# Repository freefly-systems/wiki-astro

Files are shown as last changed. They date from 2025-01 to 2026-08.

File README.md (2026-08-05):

# Astro / Astro Max

{% embed url="https://youtu.be/W2aNijm3UPw" %}

The Freefly Astro is a compact professional multi-rotor built for enterprise and industrial work. Flown with the Pilot Pro controller, it runs an enterprise PX4-based flight stack and carries an onboard mission computer, RTK-capable GNSS, and swappable payloads.

This guide will be continuously updated with the latest information.

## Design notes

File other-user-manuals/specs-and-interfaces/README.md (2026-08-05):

---
description: How to integrate Astro intro your custom workflow
icon: bolt
---

# Specs and Interfaces

{% content-ref url="technical-specs.md" %}
[technical-specs.md](technical-specs.md)
{% endcontent-ref %}

{% content-ref url="performance.md" %}
[performance.md](performance.md)
{% endcontent-ref %}

{% content-ref url="drawings-and-cad.md" %}
[drawings-and-cad.md](drawings-and-cad.md)
{% endcontent-ref %}

{% content-ref url="../compliance/" %}
[compliance](../compliance/)
{% endcontent-ref %}

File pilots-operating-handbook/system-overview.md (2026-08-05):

---
icon: book-open-lines
---

# System Overview

<figure>media&token=5d01687a-c96d-4a51-b992-1f1958ca7538"<figcaption></figcaption></figure>

Astro is the next generation of Freefly aircraft, which emphasizes expandability and customization to make sure it can stand up to all challenges thrown its way while still being the reliable workhorse drone that Freefly pilots know and love.

## Key Components

### Astro Aircraft Layout

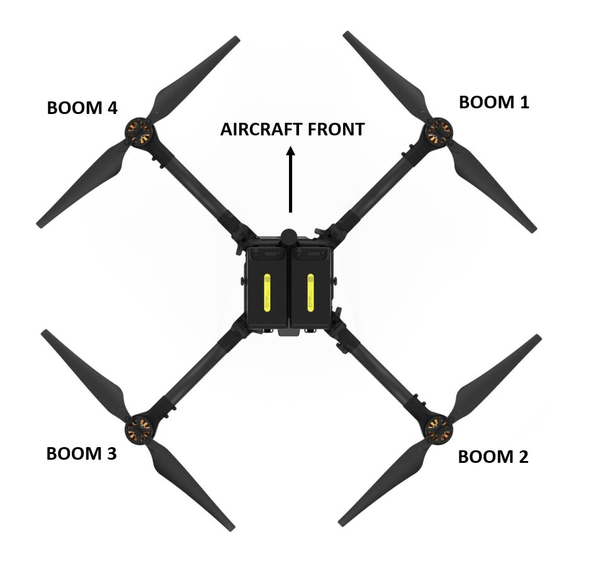
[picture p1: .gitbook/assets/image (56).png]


### Astro Transmitter

{% tabs %}
{% tab title="Pilot Pro" %}
The current iteration of Astro ships with [**Pilot Pro**](https://store.freeflysystems.com/products/pilot-pro)**,** our custom controller. For more information, check the [Pilot Pro wiki](https://freefly.gitbook.io/pilot-pro-public/).

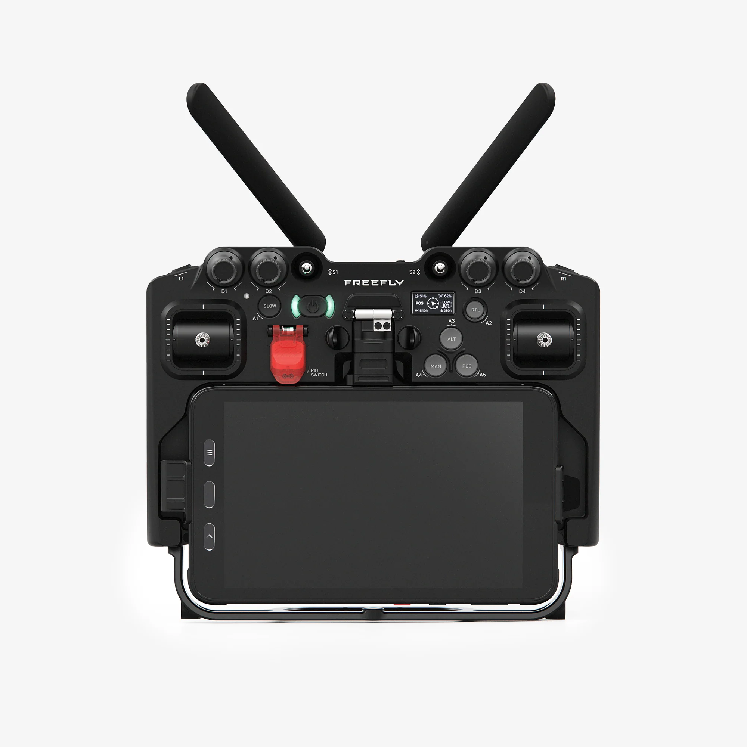
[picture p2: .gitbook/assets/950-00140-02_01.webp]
<figure><figcaption></figcaption></figure>
{% endtab %}

{% tab title="Herelink Controller" %}
Astro shipped with the [Herelink](../other-user-manuals/ecosystem/components/pilot-handsets/#herelink) controller as the pilot handset before late 2023. It runs a custom version of [Auterion Mission Control](essential-software/auterion-mission-control/) as its flight software.

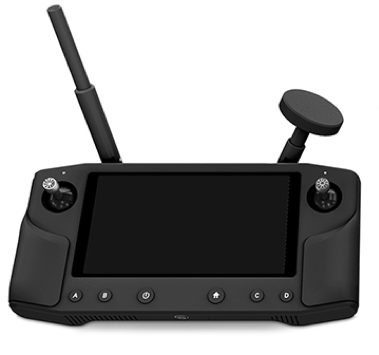
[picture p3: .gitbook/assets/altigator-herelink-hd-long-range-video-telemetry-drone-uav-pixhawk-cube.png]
<figure><figcaption></figcaption></figure>
{% endtab %}
{% endtabs %}

### SuperLight Battery

<figure>media&token=274368b1-176e-472b-a856-2636772e2193"<figcaption></figcaption></figure>

SuperLight Lithium-ion batteries are designed and manufactured by Freefly. You can find more information on the battery in the [SuperLight Battery](https://docs.freeflysystems.com/ecosystem/power/superlight-batteries) section of the wiki.

## Astro LEDs

There are 5 total status LEDs on the Astro. The 4 boom LEDs at the end of each arm show constant lights in most circumstances. By default, the rear two boom LEDs are red, and the front two boom LEDs are green. These LEDs will blink as the battery gets low, and blink quickly if there is an error.

The Astro uses a multi-color status indicator LED to communicate aircraft status on the ground. This LED is located on the front-left boom of the aircraft (pictured below in blue on boom 4). See the table below for complete information on the color codes

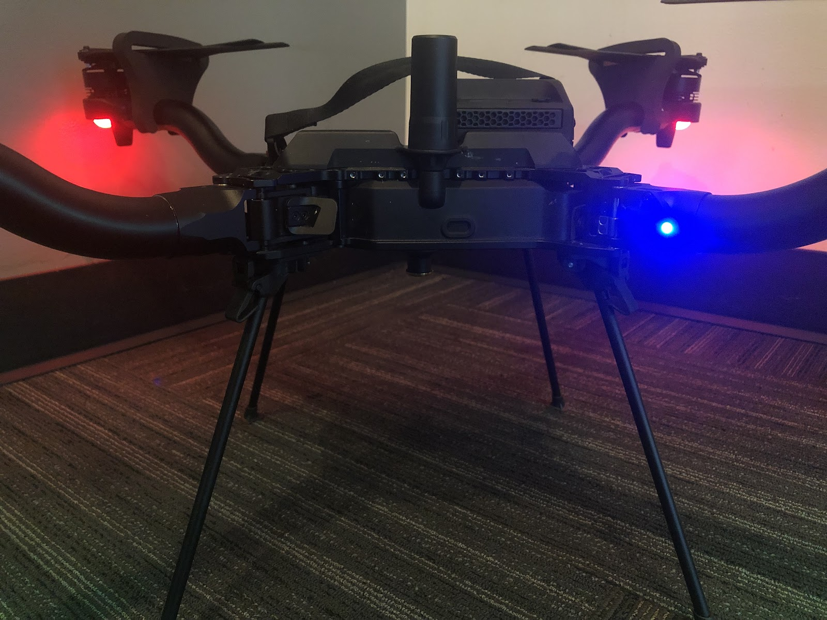
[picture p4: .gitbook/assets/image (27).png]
color code
<figure><figcaption><p>Location of the Status Indicator LED (Blue)</p></figcaption></figure>

### Status Indicator LED Color Codes

<table data-search="false"><thead><tr><th>Color</th><th>Meaning</th><th>Detail</th></tr></thead><tbody><tr><td>Solid Blue</td><td>Armed, No GPS Lock</td><td>Indicates vehicle has been armed and has no position lock from the GPS. Position, Mission and Return flight modes are not available.</td></tr><tr><td>Pulsing Blue</td><td>Disarmed, No GPS Lock</td><td>Indicates vehicle is disarmed and has no position lock from the GPS. Position, Mission and RTL flight modes will not be available until GPS lock is acquired.</td></tr><tr><td>Solid Green</td><td>Armed, GPS Lock</td><td>Indicates vehicle has been armed and has position lock from the GPS. All flight modes are available.</td></tr><tr><td>Pulsing Green</td><td>Disarmed, GPS Lock</td><td>Indicates vehicle is disarmed and has position lock from the GPS. All flight modes will be available.</td></tr><tr><td>Solid Purple</td><td>Failsafe Mode</td><td>Indicates an error has been encountered during flight and the vehicle will activate the Failsafe Action (Return To Launch by default).</td></tr><tr><td>Solid Amber</td><td>Low Battery Warning</td><td>Indicates a battery voltage below threshold.</td></tr><tr><td>Flashing Red</td><td>Error / Setup Required</td><td>Indicates an error, typically an issue with sensor calibration or autopilot configuration. </td></tr></tbody></table>

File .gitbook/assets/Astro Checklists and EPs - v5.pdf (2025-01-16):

Astro Checklists and EPs - v5

1

Before Leaving | | On Return
Astro | Packed | Clean | Everything
Batteries | Charged, Packed | Batteries | Store or charge
Herelink | Charged, Packed | Suite | Verify logs uploaded
Payload | Packed
Computer (optional) | Charged, Packed

Computer tripod (optional)Packed
RTK (optional) | Packed
RTK cable (optional) | Packed
RTK Tripod (optional) | Packed
Setup | | Tear Down
Airspace | Verify available | Flight Batteries | Remove
Astro | Remove from case | Propellers | Fold
Booms | Unfold and lock | Prop-tectors | Install, slide to motor
Prop-tectors | Remove | Booms | Fold
Motors and Props | Spin freely, No Play | Payload | Remove
Payload | Install, configure | Astro | Insert into case
Herelink | Open AMC | Suite | Annotate flights

Pilot Computer, optional Open AMC

| Connect to HereLink
| Connect RTK (optional)

Astro Checklists and EPs - v5

2

Preflight | Emergency Procedures
Herelink Battery above 20% | Low Battery
Pilot Computer Battery above 20% | Aircraft Land
Aircraft position Away from obstacles | Loss of Orientation
Payload Secure | Control Inputs Neutralize
Flight Batteries Charge > 20% | Flight Mode Position
Install and activate | Yaw Nose away
Aircraft Stationary while booting | Roll Small input
Orientation LEDs Dim, Constant | Verify direction
AMC Verify connected | Unexpected Behavior
No warnings | Control Inputs Neutralize
Return altitude set | Flight Mode Position
Geofence (optional) | Aircraft Land
Flight Mode Return, Altitude | Landing Detector Failure
Flight Mode Position | Flight Mode Position or Altitude
Aircraft Verify orientation | Land firmly
Props Verify clear | Flight Mode Manual
Takeoff | Land firmly
Throttle Down + Right (Arm) | Throttle Down + Left, 10 sec
Motors All spin | Loss of Video Signal
Orientation LEDs Bright, Constant | Flight Mode Position
Throttle Advance above center | Visual contact Establish
Astro Climb | Aircraft Orient for reception
Landing | Flight Mode Return
Announce "Landing" | RC Loss of Signal (LOS)
Landing Area Verify clear | Herelink Check Battery
Mode Switch Position | Check Antennas
Astro Touchdown | Flight Mode Return
Throttle Down (Disarm) | Emergency Stop - Manual
Motors All Stop | Flight Mode Manual
Orientation LEDs Dim, Constant | Throttle Down + Left, 10 sec
Post Flight | Emergency Stop - AMC
AMC Check for warnings | AMC App Tap "Armed" (top center)
Aircraft, Props, Motors Inspect for Damage | Hold to confirm E-Stop

Flight Batteries Remove

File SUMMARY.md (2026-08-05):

# Table of contents

* [Astro / Astro Max](README.md)

## Pilot's Operating Handbook

* [Getting Started](pilots-operating-handbook/getting-started.md)
* [System Overview](pilots-operating-handbook/system-overview.md)
* [Flight Part 1 - Flight Modes](pilots-operating-handbook/flight-modes.md)
* [Flight Part 2 - Operation](pilots-operating-handbook/operation.md)
* [Flight Part 3 - Emergency / Advanced](pilots-operating-handbook/emergency-procedures.md)
* [Auterion Software](pilots-operating-handbook/essential-software/README.md)
  * [Auterion Mission Control](pilots-operating-handbook/essential-software/auterion-mission-control/README.md)
    * [AMC - Fly](pilots-operating-handbook/essential-software/auterion-mission-control/amc-fly.md)
    * [AMC - Plan](pilots-operating-handbook/essential-software/auterion-mission-control/amc-plan/README.md)
      * [Transfer Mission Plan and KML Files with Herelink](pilots-operating-handbook/essential-software/auterion-mission-control/amc-plan/transfer-mission-plan-and-kml-files-with-herelink.md)
      * [Terrain Follow](pilots-operating-handbook/essential-software/auterion-mission-control/amc-plan/terrain-follow.md)
      * [Offline Maps](pilots-operating-handbook/essential-software/auterion-mission-control/amc-plan/offline-maps.md)
    * [AMC - Vehicle Setup](pilots-operating-handbook/essential-software/auterion-mission-control/amc-vehicle-setup/README.md)
      * [Advanced Vehicle Setup](pilots-operating-handbook/essential-software/auterion-mission-control/amc-vehicle-setup/advanced-vehicle-setup.md)
      * [Parameters](pilots-operating-handbook/essential-software/auterion-mission-control/amc-vehicle-setup/parameters.md)
    * [AMC - Photos](pilots-operating-handbook/essential-software/auterion-mission-control/amc-photos.md)
    * [AMC - User Account](pilots-operating-handbook/essential-software/auterion-mission-control/amc-user-account.md)
    * [AMC - Settings](pilots-operating-handbook/essential-software/auterion-mission-control/amc-settings/README.md)
      * [Advanced Mode](pilots-operating-handbook/essential-software/auterion-mission-control/amc-settings/advanced-mode.md)
  * [Auterion Suite](pilots-operating-handbook/essential-software/auterion-suite.md)
* [Pro Tips and Limitations](pilots-operating-handbook/limitations.md)
* [Getting Technical Support](pilots-operating-handbook/getting-technical-support.md)

## Maintenance

* [Standard Maintenance Procedures](maintenance/standard-maintenance-procedures/README.md)
  * [Periodic Maintenance](maintenance/standard-maintenance-procedures/periodic-maintenance.md)
  * [Replacing Components](maintenance/standard-maintenance-procedures/replacing-components/README.md)
    * [Replacing Propellers](maintenance/standard-maintenance-procedures/replacing-components/replacing-propellers.md)
    * [Installing a SIM Card](maintenance/standard-maintenance-procedures/replacing-components/installing-a-sim-card.md)
  * [Calibration and Tuning](maintenance/standard-maintenance-procedures/calibration-and-tuning.md)
  * [Controller / Radio Binding](maintenance/standard-maintenance-procedures/controller-radio-binding.md)
  * [SL8/Astro Battery Connectors](maintenance/standard-maintenance-procedures/sl8-astro-battery-connectors.md)
* [Network and Connectivity](maintenance/network-and-connectivity.md)
* [Software Updates](maintenance/software-release-notes/README.md)
  * [Updating Firmware](maintenance/software-release-notes/software.md)
  * [Astro Software v2.2 - What's New](maintenance/software-release-notes/astro-software-v2.2-whats-new.md)
  * [Astro Software v2.0 - What's New](maintenance/software-release-notes/astro-software-v2.0-whats-new.md)
  * [Astro Software v1.7 - What’s New](maintenance/software-release-notes/astro-software-v1.7-whats-new.md)
  * [Astro Software v1.4 - What’s New](maintenance/software-release-notes/astro-software-v1.4-whats-new.md)
  * [Astro Software v1.2 - What’s New](maintenance/software-release-notes/astro-software-v1.2-whats-new.md)
* [FAQ & Troubleshooting](maintenance/faq-and-troubleshooting.md)

## Other User Manuals

* [Ecosystem](other-user-manuals/ecosystem/README.md)
  * [Components](other-user-manuals/ecosystem/components/README.md)
    * [Batteries](other-user-manuals/ecosystem/components/batteries.md)
    * [Pilot Pro Controller](other-user-manuals/ecosystem/components/pilot-pro-controller.md)
    * [Herelink Handset (Legacy)](other-user-manuals/ecosystem/components/pilot-handsets/README.md)
      * [Herelink Controller Maintenance](other-user-manuals/ecosystem/components/pilot-handsets/herelink-controller-maintenance/README.md)
        * [Updating Herelink Software](other-user-manuals/ecosystem/components/pilot-handsets/herelink-controller-maintenance/updating-herelink-software.md)
        * [Switching to Freefly Updater](other-user-manuals/ecosystem/components/pilot-handsets/herelink-controller-maintenance/switching-to-freefly-updater.md)
        * [Removing/Reinstalling the Herelink Cover](other-user-manuals/ecosystem/components/pilot-handsets/herelink-controller-maintenance/removing-reinstalling-the-herelink-cover.md)
    * [Vibration Isolators](other-user-manuals/ecosystem/components/vibration-isolators.md)
    * [Skyview Payload Mount](other-user-manuals/ecosystem/components/skyview-payload-mount.md)
    * [GNSS Base Stations](other-user-manuals/ecosystem/components/gnss-base-stations.md)
  * [Development Tools](other-user-manuals/ecosystem/development-tools/README.md)
    * [MavSDK](other-user-manuals/ecosystem/development-tools/mavsdk.md)
    * [Software Interfaces](other-user-manuals/ecosystem/development-tools/software-interfaces.md)
    * [Payload Mounting Interfaces](other-user-manuals/ecosystem/development-tools/payload-mounting-interfaces.md)
    * [Electrical Interfaces](other-user-manuals/ecosystem/development-tools/electrical-interfaces.md)
    * [Onboard Computer](other-user-manuals/ecosystem/development-tools/onboard-computer.md)
  * [Esri ArcGIS Flight (Site Scan)](other-user-manuals/ecosystem/esri-arcgis-flight-site-scan/README.md)
    * [1 - Setup and Connecting to Astro](other-user-manuals/ecosystem/esri-arcgis-flight-site-scan/1-setup-and-connecting-to-astro.md)
    * [2 - Preflight and Mission Planning](other-user-manuals/ecosystem/esri-arcgis-flight-site-scan/2-preflight-and-mission-planning.md)
    * [3 - Flying a Mission with Astro](other-user-manuals/ecosystem/esri-arcgis-flight-site-scan/3-flying-a-mission-with-astro.md)
    * [4 - Post-Flight and Image Processing](other-user-manuals/ecosystem/esri-arcgis-flight-site-scan/4-post-flight-and-image-processing.md)
    * [Global Settings](other-user-manuals/ecosystem/esri-arcgis-flight-site-scan/global-settings.md)
  * [DroneDeploy](other-user-manuals/ecosystem/dronedeploy.md)
* [Specs and Interfaces](other-user-manuals/specs-and-interfaces/README.md)
  * [Technical Specs](other-user-manuals/specs-and-interfaces/technical-specs.md)
  * [Performance](other-user-manuals/specs-and-interfaces/performance.md)
  * [Drawings and CAD](other-user-manuals/specs-and-interfaces/drawings-and-cad.md)
* [Travel and Shipping](other-user-manuals/travel-and-shipping.md)
* [Compliance](other-user-manuals/compliance/README.md)
  * [FAA Remote Identification (RID)](other-user-manuals/compliance/faa-remote-identification-rid.md)
  * [DIU Blue sUAS](other-user-manuals/compliance/diu-blue-suas.md)
* [Legal](other-user-manuals/legal.md)

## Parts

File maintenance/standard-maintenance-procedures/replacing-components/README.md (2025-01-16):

# Replacing Components

{% content-ref url="../../../other-user-manuals/ecosystem/components/pilot-handsets/herelink-controller-maintenance/removing-reinstalling-the-herelink-cover.md" %}
[removing-reinstalling-the-herelink-cover.md](../../../other-user-manuals/ecosystem/components/pilot-handsets/herelink-controller-maintenance/removing-reinstalling-the-herelink-cover.md)
{% endcontent-ref %}

{% content-ref url="replacing-propellers.md" %}
[replacing-propellers.md](replacing-propellers.md)
{% endcontent-ref %}

{% content-ref url="installing-a-sim-card.md" %}
[installing-a-sim-card.md](installing-a-sim-card.md)
{% endcontent-ref %}

## Replacement Parts

If you need to purchase spare or replacement parts, please go to [store.freeflysystems.com](http://store.freeflysystems.com) to purchase our standard parts.&#x20;

For any specific replacement needs or issues, please contact support@freeflysystems.com or [submit a direct ticket](https://freeflysystems.com/contact) with your request.

## Fastener Specifications

{% hint style="warning" %}
**Use Of Thread locker**

Bolts and screws used in the daily use of this aircraft do not require threadlocking compound. This includes the screws securing the vibration isolation system and the  landing gear parts.

However, for the structural fasteners described in parts of this section, blue Loctite 243 compound or equivalent is required. Apply sparingly to the threads before insertion.
{% endhint %}

{% hint style="warning" %}
**Fastener Installation**

The Freefly hex drivers included with Astro are designed to limit the torque that can be applied to each bolt or screw and help prevent stripping the fastener head.

Thread all fasteners into their respective holes until snug (when the fastener head bottoms out and lightly clamps the two mating parts together).

To prevent excessive tightening and damaging the fastener or parts, twist the driver from the smaller diameter knurled section of the tool between your thumb and index finger for small fasteners (under size M3) or with your thumb and two forefingers for larger fasteners (size M3 and larger).
{% endhint %}

#### Fastener Torque Values

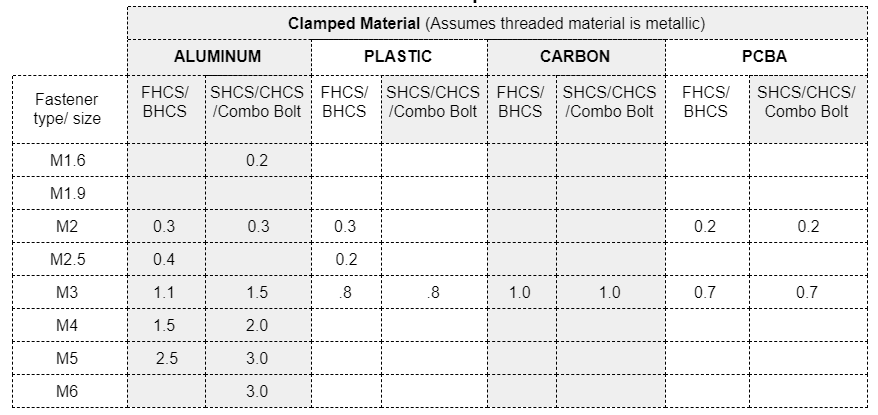
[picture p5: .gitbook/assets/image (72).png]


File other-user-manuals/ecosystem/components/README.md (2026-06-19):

# Components

{% content-ref url="batteries.md" %}
[batteries.md](batteries.md)
{% endcontent-ref %}

{% content-ref url="pilot-handsets/" %}
[pilot-handsets](pilot-handsets/)
{% endcontent-ref %}

{% content-ref url="vibration-isolators.md" %}
[vibration-isolators.md](vibration-isolators.md)
{% endcontent-ref %}

{% content-ref url="gnss-base-stations.md" %}
[gnss-base-stations.md](gnss-base-stations.md)
{% endcontent-ref %}

{% content-ref url="../../../maintenance/standard-maintenance-procedures/replacing-components/replacing-propellers.md" %}
[replacing-propellers.md](../../../maintenance/standard-maintenance-procedures/replacing-components/replacing-propellers.md)
{% endcontent-ref %}

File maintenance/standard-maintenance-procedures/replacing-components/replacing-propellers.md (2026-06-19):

# Replacing Propellers

{% embed url="https://www.youtube.com/watch?v=ifPETgSw0Oc" %}

{% hint style="warning" %}
Ensure rotation direction is correct. Always replace propellers with a set intended to rotate in the same direction (clockwise or counter-clockwise). We suggest replacing one propeller assembly at a time to minimize potential for mix-ups, rather than removing all propellers at once.
{% endhint %}

{% hint style="info" %}
Always replace both propeller blades as a set. They are a matched and balanced pair, with matching serial numbers. This is to reduce vibration.
{% endhint %}

#### Astro vs Astro Max Motors

Before you consider replacing props, it is important to identify the which Astro motors you have.&#x20;

The **Astro** is equipped with Freefly _F45_ motors, where the **Astro Max** has a newer Freefly _7010_ motor.

In addition to providing more thrust than the prior generation motor, the Astro Max 7010 motors have a different mounting pattern for props than the F45 motor. Reference the image below to identify which one you have.

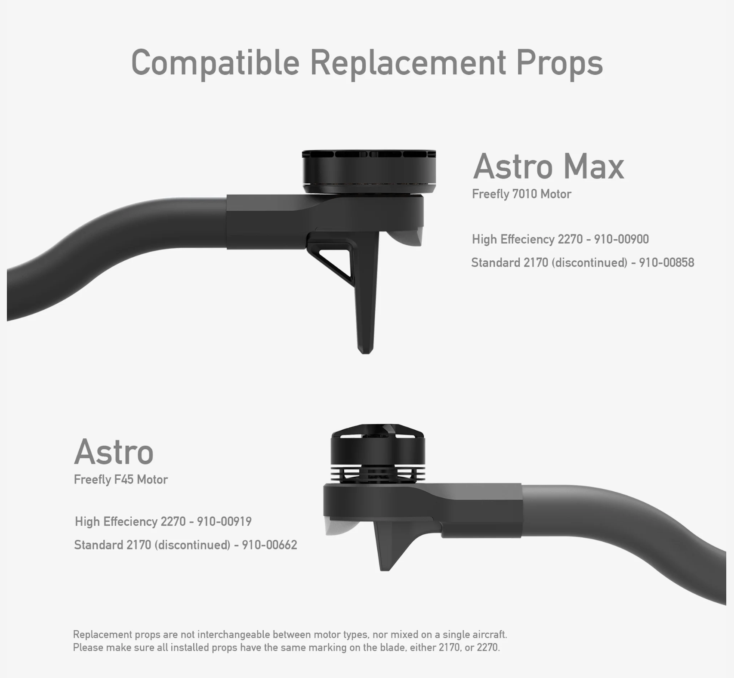
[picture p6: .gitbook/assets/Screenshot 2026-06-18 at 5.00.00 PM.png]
<figure><figcaption></figcaption></figure>

#### Identifying your current props

Legacy props are 21" long and marked with "2170".

High efficiency props are 22" long, and marked with "2270".&#x20;

Example of a 2270 CCW prop:\
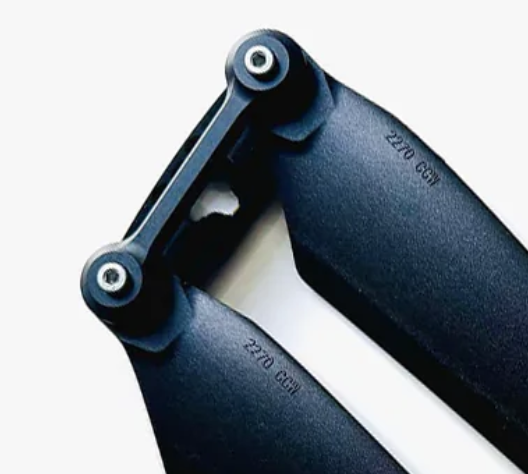
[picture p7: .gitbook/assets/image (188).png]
&#x20;

#### **Which props do I need?**

* Since we no longer sell the 21" (2170) props, we only carry the high-efficiency 22" (2270) props.
* Depending on the motor you have, the 22" props will come with the appropriate mounting hardware.
  * If you have the Astro with F45 motors, you have the legacy Astro and will need to get the [Astro Legacy Spare Props](https://store.freeflysystems.com/collections/astro/products/astro-legacy-spare-propeller-set-2270-high-efficiency) (2270)
  * If you have the Astro with 7010 motors, you have Astro Max, and will need to get the [Astro Max Spare Props](https://store.freeflysystems.com/collections/astro/products/astro-max-spare-propeller-set-high-efficiency) (2270)<br>

#### How many props do I need?

1. If you want to upgrade your legacy Astro (F45 motors) to maximize flight time, you'll need to purchase two sets of the 2270 props. We recommend a third set to have a spare set in your kit.
2. If you just need a replacement prop (CW or CCW) and have 21" props on your Astro marked with "2170" on the blade, you'll need to purchase two sets of the 2270 props so you can replace the props on all four motors.&#x20;
3. If your Astro already has 22" props marked with "2270" on the blade, just purchase what you feel comfortable having for spares. Most people have one set (one each CW & CCW) in their kit.&#x20;

#### Steps to replace props on legacy Astro (F45 motors)

1. Remove fasteners between the prop hub and the motors: (x4) M3x10 bolts.
2. Remove the old propeller assembly.
3. Fit the new propeller assembly.
4. Apply Loctite 243 or equivalent to all screws before installing. torque to 1.5 Newton meters.
5. Reinstall (x4) M3x8 bolts.

<figure>media&token=7237d1a8-d1b5-465c-ac06-25bf0994b76e"<figcaption><p>Propellers are labelled with their orientation, Clockwise (CW) or Counter-clockwise (CCW).</p></figcaption></figure>

The correct direction of the propellers is shown below. Please note the arrow indicating the front of the Astro, which is easily identified by the cylindrical antenna.

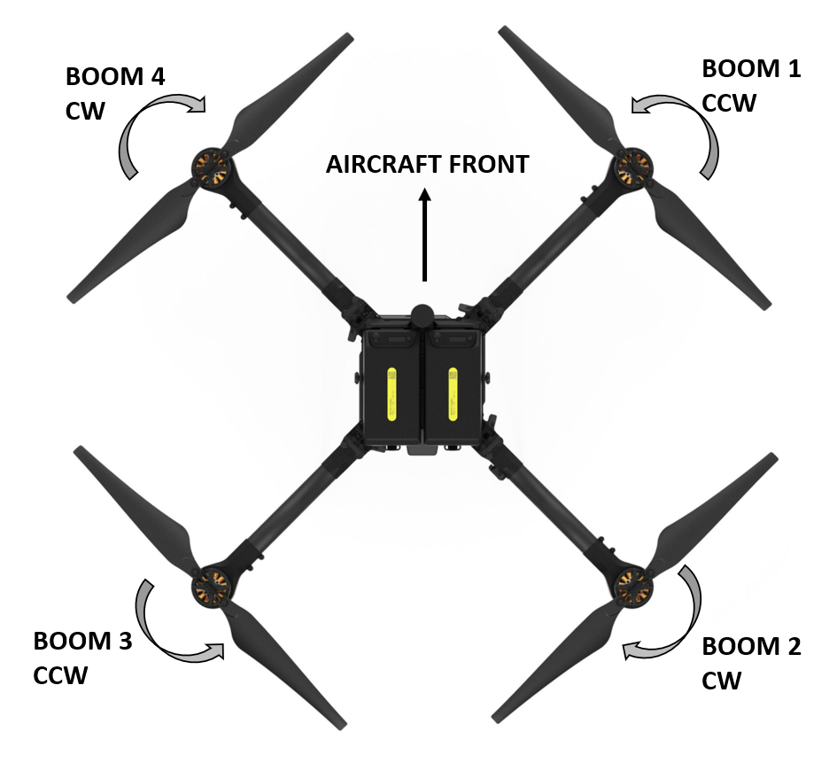
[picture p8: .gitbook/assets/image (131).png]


### Prop Tension

Each blade of the propeller assembly should move freely with a small amount of resistance. It should not be difficult to fold the prop manually, and the force of gravity should be enough to pivot the blade at the bolt if the aircraft is rotated.

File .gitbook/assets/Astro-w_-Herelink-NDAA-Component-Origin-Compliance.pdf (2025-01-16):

# Astro w /Herelink NDAA sec. 848 Compliance Specification Sheet

Specified Components | Sub component | Specific Product Used | Supplier | Country | Included | Required | Assembly | Testing | Validation
Flight controller | Flight controller hardware | Skynode | Freefly | Taiwan | Yes | Yes | Taiwan | USA | USA
| Flight control firmware | Firmware | Freefly | USA | Yes | Yes | N/A | USA | USA
Radios | Control & Video Transmitter/Receiver | Herelink | ProfiCNC | China | Yes | Yes | ProfiCNC | USA | USA
Data transmission devices | LTE Modem | Skynode | Freefly | Taiwan | Yes | No* | Taiwan | USA | USA
Cameras | N/A | N/A | N/A | N/A | N/A | N/A | N/A | N/A | N/A
Ground control system | Pilot Controller | Herelink | ProfiCNC | China | Yes | Yes | N/A | USA | USA
| Ground Station Computer (operator supplied) | Computer or tablet | Operator supplied | N/A | No | No | N/A | N/A | N/A
Operating software | Pilot’s Control Software | Auterion Mission Control | Auterion | Switzerland | Yes | No | N/A | Auterion | Auterion
Network connectivity | LTE | T-Mobile SIM | T-Mobile | Various | Yes | No | Various | Various | Various
Data storage | Local log storage | microSD card | Sandisk | Various | Yes** | Yes | Various | USA | USA
| Cloud Storage | Auterion Suite | Auterion | Switzerland | No | No | N/A | USA | USA

### *LTE Connectivity is data plan based and is not required for operation **SD card is for local storage only and is not physically accessible to users

## July 12th, 2021

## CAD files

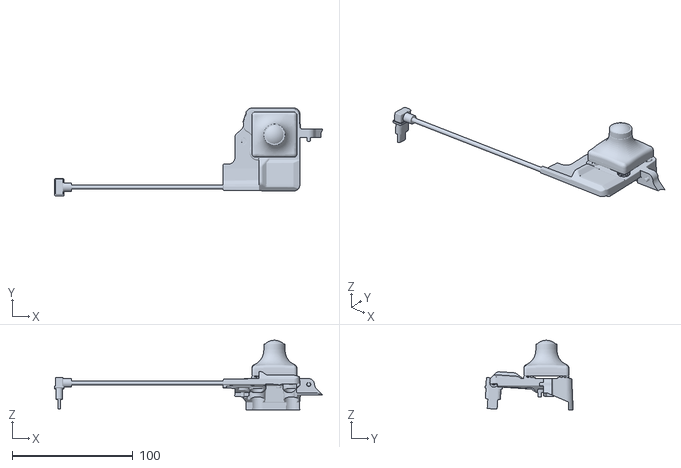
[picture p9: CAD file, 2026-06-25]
.gitbook/assets/Astro FPV System.STL
221.6 x 73.0 x 57.5

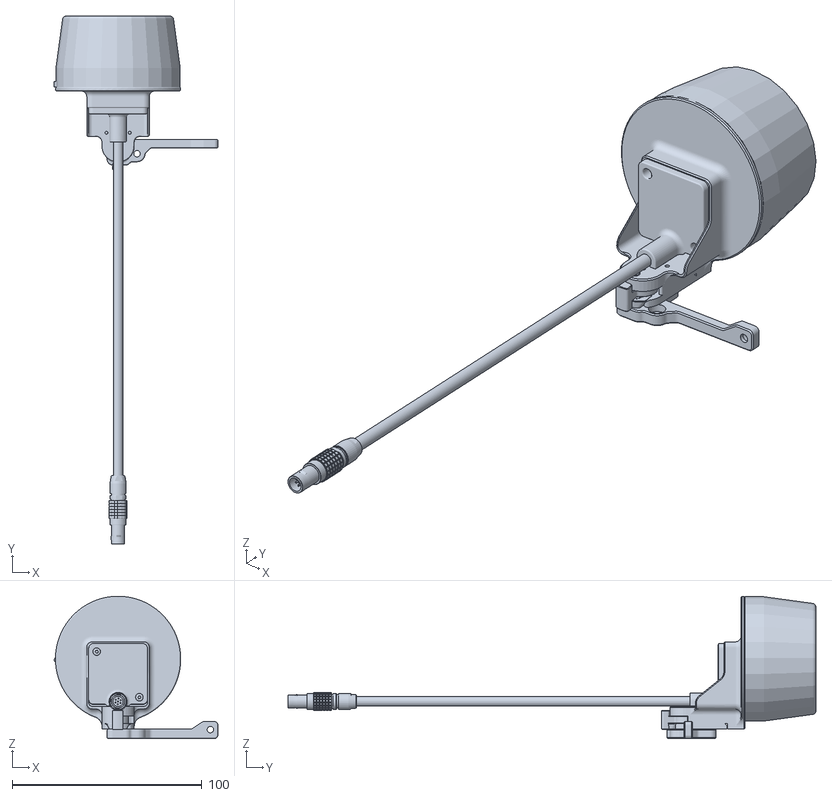
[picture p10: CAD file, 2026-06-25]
.gitbook/assets/Flux GNSS Module and Astro Mount.STL
86.4 x 278.1 x 75.1

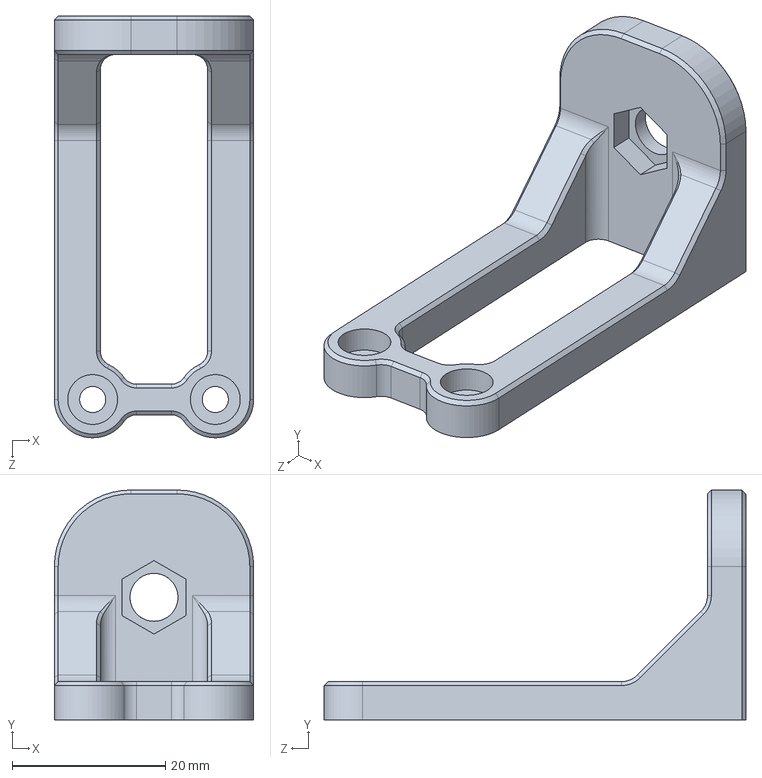
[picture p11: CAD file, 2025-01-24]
.gitbook/assets/432-00086 Antenna Mount Astro REV_01.STEP
26.0 x 30.0 x 55.0 mm

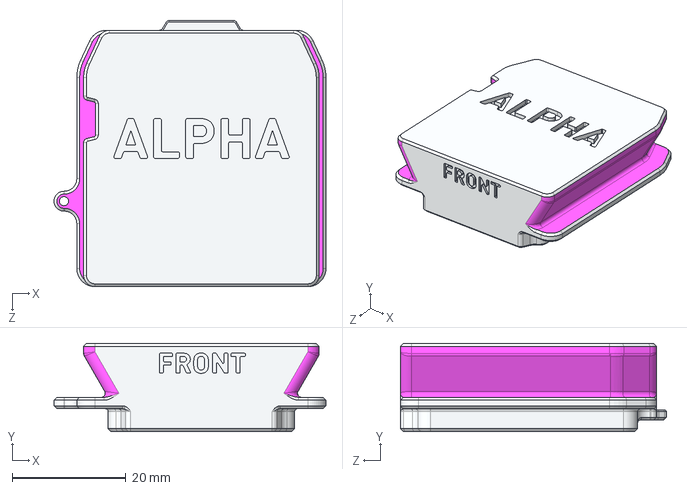
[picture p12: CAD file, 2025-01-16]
.gitbook/assets/ALPHA_410-01094 Dovetail Mount Universal with Passthrough.STEP
47.8 x 15.5 x 46.8 mm

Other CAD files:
.gitbook/assets/432-00086 Antenna Mount Astro REV_01.STL

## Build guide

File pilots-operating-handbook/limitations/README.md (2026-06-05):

# Pro Tips and Limitations

It is possible to operate Astro close to the limits of performance by maintaining awareness of the performance envelope, how the aircraft behaves if the limits are exceeded, and best practices for operating in harsh environments.

This page reflects the limitations of the most current version. As the Astro platform matures, limitations are likely to change. For major changes that may affect these limitations, check the [release notes](https://freefly.gitbook.io/astro-public/products/astro/maintenance-manual/software-release-notes).

***

## Troubleshooting

Visit our [Troubleshooting Spreadsheet](https://docs.google.com/spreadsheets/d/1DXkk0BmRx9qLbjpBt2KgKYFOQhEGUTcyyQB6rOmb4ac/edit#gid=528435697) to look into additional solutions if you aren't finding what you're looking for on the wiki.&#x20;

***

## Flight Control

For all flight modes except Manual, at altitudes below 2 meters, the tilt angle is reduced to 12 degrees and vertical speed is reduced to 0.7 m/s.

The purpose is to prevent tip-overs while landing but has the side effect of reducing speed if flying below the takeoff point (e.g. surveying from a high vantage point). We are working to correct this behavior.

***

## Continuous Flight

If you have 8 SL8 batteries, 6 SL8 chargers, and electricity at the location of your flight, you can continuously charge 6 batteries at a time while flying Astro, allowing for uninterrupted flight for as long as you need. If you are flying without a payload, you will only need 6 batteries and 4 chargers.&#x20;

{% hint style="warning" %}
In hot conditions, you will likely need an additional 2 batteries, as it may take some time to cool the recently flown batteries to an acceptable charging temperature (50°C).&#x20;
{% endhint %}

***

## Radio Range and Interferences

Operating with a weak signal, whether due to interference or long range, can cause loss of link with the aircraft, which will engage failsafes. If you anticipate a weak signal situation, double-check that failsafes are set appropriately.

### Range

The range of Herelink and the Doodle radios on Astro is approximately 2 km in ideal conditions, assuming there are no interferences and the antennas are positioned correctly.

### Antenna Positioning

{% hint style="warning" %}
This is one of the simplest to miss and impact the range of the flight
{% endhint %}

#### **Pilot Pro**

Both the Doodle and Herelink radio modules on Pilot Pro use two blade antennas that are omni directional. It is important to follow these basic guidelines:

* Antennas should both point in the same direction.&#x20;
* Antennas should point towards ground for best signal quality in most situations.

<figure><figcaption></figcaption></figure>

#### **Herelink GCS (Legacy):**&#x20;

Herelink GCS has two types of antennas.&#x20;

* Patch antenna (with a circular disk on top) is a directional antenna and should be pointed toward the aircraft
* Other antenna is omni-directional and it should be positioned pointing towards the ground or sky

### Interferences

Range can be reduced by radio interference from other sources like wifi networks. Obstacles like trees and buildings in close proximity to the controller or Astro, as well as directly between the two, can dramatically reduce range.

### Multiple Aircraft

* Astro's Doodle radio configuration runs on dedicated peer to peer channels. In order to fly multiple Astros in the same airspace, make sure to scan channels and then set each Astro Doodle to a different channel.
* Astro's Herelink radios are channel hopping by default. 4 aircraft can fly simultaneously in the same airspace in practice. If more aircraft are present, interference can cause loss of radio link and control.
  * If using the legacy Herelink GCS, you can set each Herelink to be on a dedicated channel
  * If using the Pilot Pro with the Herelink radio, this feature is not yet available.

### High Power Radio Interference

Avoid using high-power, low-frequency radio transmitters (such as the RFD 900) mounted to Astro, as it can disrupt the normal function of the aircraft. For more information,  see this [service bulletin](https://freeflysystems.com/knowledge-base/astro-sb002-high-power-radio-astro-interference).&#x20;

***

## Environment

### Temperature

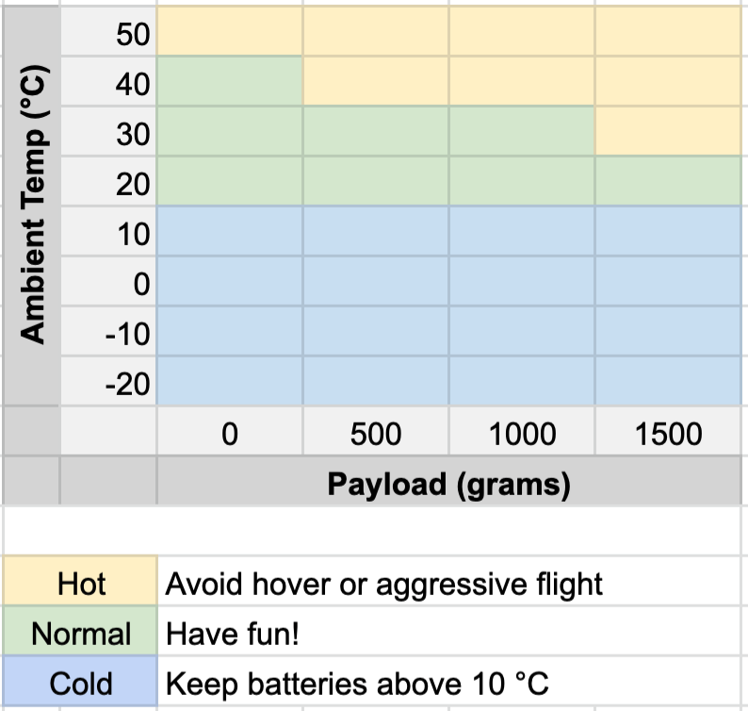
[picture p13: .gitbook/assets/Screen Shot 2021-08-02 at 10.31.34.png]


Astro can operate between -20 and 50 C. Position mode and survey flying are normal throughout the range. However, care is needed to operate at low and high temperatures.

Yellow region: Hovering and aggressive flights may give overtemp warnings. Follow the warning instructions.

Blue region: If batteries become too cold, state of charge will decline quickly and aircraft will enter Return or Land mode. Keep batteries warm, above 10 °C at takeoff, then self-heating will keep them warm.&#x20;

{% tabs %}
{% tab title="Tips for operating in hot environments" %}
At high temperatures, the limiting factors are motor and battery temperatures. AMC will display a warning if the motors or batteries become too hot. Heed the warnings! Astro operates normally in forward flight up to 15 m/s with a full payload of 1500 grams.&#x20;

Cooling air is your friend. The motors get much more cooling air in forward flight than in a hover. Overheat errors may occur when hovering because there is less airflow, or when flying aggressively because heating increases with current.

Batteries may require cooling before charging. Bring an extra set of batteries and chargers to enable continuous flying. If you connect batteries to the charger while cooling, they will automatically begin charging as soon as they have cooled sufficiently.

Keep the equipment out of prolonged direct sunlight, especially the Herelink. Herelink will shut down if it overheats, and it does not give a warning.
{% endtab %}

{% tab title="Tips for operating in cold environments" %}
At low temperatures, the battery cell temperature is the key limiting factor. When the cells themselves are below 10 °C (ambient air can be down to -20 °C), the built-in battery management system's (BMS) state of charge (SoC) algorithm has reduced accuracy. The SoC may decrease to zero suddenly. If this happens, [low battery failsafes](../emergency-procedures.md#low-battery) (RTL and Land) will be triggered, causing the aircraft to climb or descend suddenly.

These failsafes can be overridden by selecting another flight mode (override by moving the sticks is not available during a failsafe). The battery will not cut off power output in the air, however low temperatures generally reduce capacity which will reduce flight time.

If the batteries are 10 °C or warmer at the start of a flight, heating from discharge will keep them warm enough to fly.

To keep batteries warm, charge them in a heated environment and store them in an insulated container (a cooler works well)**In rare cases propellers can experience icing, this occurs when ice begins to form on the tips and underside of the blades due to temperature and humidity. This will cause the props to become unbalanced, increasing drag and reducing lift. Flying with iced blades can be dangerous and is not advised.**
{% endtab %}
{% endtabs %}

{% hint style="info" %}
Keep the Herelink handset out of direct sunlight. It can operate at up to 50C ambient _if its plugged in for charging and in the shade._ \
\
For the best performance in hot or cold weather, we recommend charging the Herelink during use. Under very hot or cold weather Herelink's battery performance can drop quickly and can cause it to shutdown.
{% endhint %}

{% hint style="warning" %}
Herelink will shut down if the internal temperature increases over 55C, and it does not give a warning. Direct sunlight can increase the temperature of the Herelink beyond this limit very quickly.&#x20;
{% endhint %}

### Wind

Operating Astro at winds greater than 8-10m/s can be dangerous. Keep in mind that the wind speed at higher altitudes is typically much higher. In high wind, AMC will show a warning.

Flying Astro is high wind is not advised. If the wind speed is a significant fraction of [Astro's top speed](https://freefly.gitbook.io/astro-public/astro/specs-and-interfaces/performance#flight-speeds), control authority will be diminished in all flight modes.

When Astro is not flying, fold the props and install the propeller protectors. If the wind blows through open props, it can cause them to spin up dangerously.

### Rain and Dust

Astro can operate in moderate rain (approximately 3 mm per hour). [USGS has a guide (scroll to bottom)](https://water.usgs.gov/edu/activity-howmuchrain-metric.html) to help translate between forecasts like "shower" or "drizzle" to accumulation amount.

Battery connectors cannot be mated while wet or containing debris. We recommend compressed air to clean the connectors.

#### Tips for operating in Rainy and Dusty environments.

Rain in particular increases the risk of electrical malfunction because it can lead to short circuits

Dust carries a risk of mechanical malfunction because it can enter the motors and obstruct rotation.

Both of these conditions carry an increased risk of malfunction and danger. It is difficult to judge the exact amount of precipitation, and the amount can vary without warning during the course of a flight. Therefore, we recommend avoiding situations that endanger people.

***

## Voltage Mismatch

If the two batteries powering Astro have a voltage difference of more than 2.0V, a voltage mismatch error will occur. 2V is roughly a 25% difference in the batteries' states of charge.&#x20;

***

## Magnetic Interference

In a situation where there is a magnetic interference that is preventing the aircraft to figure out its heading before takeoff, you are presented with options:

* Move away from any potential sources of magnetic interference, like metal or water. In most cases, moving the Astro a few feet away will allow it to get a better magnetic reading to figure out the heading, and position mode will become available for takeoff.&#x20;
* Take off in altitude mode. Shortly after flying in altitude mode, GPS heading will be locked and you can then switch to position mode.

{% hint style="warning" %}
Be aware that flying in Altitude Mode does introduce additional risk. If the aircraft loses connection with the controller, it will not hold its horizontal position which may result in a crash if control is not re-established quickly. &#x20;
{% endhint %}

***

.

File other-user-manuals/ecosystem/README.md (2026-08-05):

---
icon: gears
---

# Ecosystem

{% content-ref url="components/" %}
[components](components/)
{% endcontent-ref %}

{% content-ref url="../../pilots-operating-handbook/essential-software/" %}
[essential-software](../../pilots-operating-handbook/essential-software/)
{% endcontent-ref %}

{% content-ref url="development-tools/" %}
[development-tools](development-tools/)
{% endcontent-ref %}

## Astro Integration Sketchpad

{% file src="../../.gitbook/assets/Astro Integration Sketchpad v1.pdf" %}
Astro Integration Sketchpad
{% endfile %}

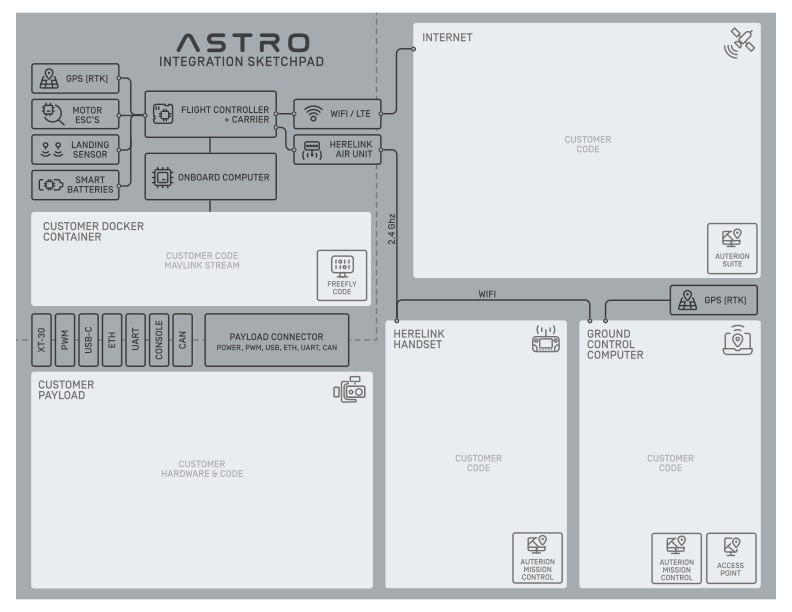
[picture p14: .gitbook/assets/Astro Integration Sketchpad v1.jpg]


Here's a printable template to diagram ideas for working with Astro. We're looking forward to [seeing your plans!](https://freeflysystems.com/contact)

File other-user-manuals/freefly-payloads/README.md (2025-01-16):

# FREEFLY PAYLOADS

{% content-ref url="lr1-payload/" %}
[lr1-payload](lr1-payload/)
{% endcontent-ref %}

{% content-ref url="a7r4-payload/" %}
[a7r4-payload](a7r4-payload/)
{% endcontent-ref %}

{% content-ref url="wiris-pro-payload/" %}
[wiris-pro-payload](wiris-pro-payload/)
{% endcontent-ref %}

{% content-ref url="ventus-ogi-payload/" %}
[ventus-ogi-payload](ventus-ogi-payload/)
{% endcontent-ref %}

{% content-ref url="fpv-camera.md" %}
[fpv-camera.md](fpv-camera.md)
{% endcontent-ref %}

{% content-ref url="workflows-maintenance-updates/" %}
[workflows-maintenance-updates](workflows-maintenance-updates/)
{% endcontent-ref %}

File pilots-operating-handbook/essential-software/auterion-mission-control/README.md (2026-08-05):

# Auterion Mission Control

Auterion Mission Control (AMC) is a ground control station application for pilots. Use it to plan and fly missions, control the aircraft in flight, and configure Astro on the ground. AMC comes pre-installed on Pilot Pro and is also available as a desktop app for PC, Mac, and Linux.&#x20;

See Auterion's full documentation for AMC [here](https://docs.auterion.com/vehicle-operation/auterion-mission-control).

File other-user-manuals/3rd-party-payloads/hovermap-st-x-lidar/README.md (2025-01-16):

# Hovermap ST-X Lidar

The Emesent Hovermap ST-X lidar is an excellent payload for creating detailed, accurate lidar point clouds.

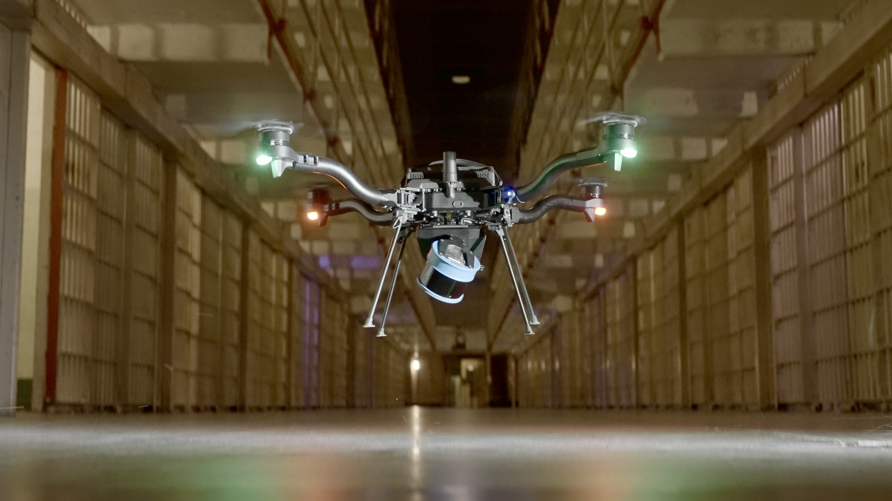
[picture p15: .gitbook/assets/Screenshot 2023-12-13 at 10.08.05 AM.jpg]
<figure><figcaption><p>Astro + Hovermap ST-X flying inside Alcatraz Cell House </p></figcaption></figure>

### Setting up Hovermap

{% content-ref url="hovermap-setup-on-astro.md" %}
[hovermap-setup-on-astro.md](hovermap-setup-on-astro.md)
{% endcontent-ref %}

### Operation modes

Hovermap can interact with Astro as a passive payload, for mapping applications that can be flown with good GPS signal in open spaces with few obstacles. &#x20;

{% content-ref url="mapping-with-hovermap.md" %}
[mapping-with-hovermap.md](mapping-with-hovermap.md)
{% endcontent-ref %}

Hovermap can also use the lidar data of the environment around Astro, and build a 3D model in real time. It can use that data for obstacle avoidance, and even allow Astro to autonomously explore GPS-denied areas like under bridges and inside tunnels and mines.&#x20;

{% embed url="https://drive.google.com/file/d/1E1IJqVptU_CEoJ5mKBL6M3PxekiDd3TQ/view?usp=drive_link" %}
Bridge scan with Hovermap ST-X
{% endembed %}

{% embed url="https://youtu.be/045shpvB-m4" %}
Astro navigating using Hovermap Assisted Mode
{% endembed %}

{% content-ref url="assisted-autonomous-flight.md" %}
[assisted-autonomous-flight.md](assisted-autonomous-flight.md)
{% endcontent-ref %}

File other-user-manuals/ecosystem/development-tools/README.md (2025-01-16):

# Development Tools

{% content-ref url="mavsdk.md" %}
[mavsdk.md](mavsdk.md)
{% endcontent-ref %}

{% content-ref url="software-interfaces.md" %}
[software-interfaces.md](software-interfaces.md)
{% endcontent-ref %}

{% content-ref url="payload-mounting-interfaces.md" %}
[payload-mounting-interfaces.md](payload-mounting-interfaces.md)
{% endcontent-ref %}

{% content-ref url="electrical-interfaces.md" %}
[electrical-interfaces.md](electrical-interfaces.md)
{% endcontent-ref %}

{% content-ref url="onboard-computer.md" %}
[onboard-computer.md](onboard-computer.md)
{% endcontent-ref %}

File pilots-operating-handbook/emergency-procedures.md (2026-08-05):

---
icon: drone-front
---

# Flight Part 3 - Emergency / Advanced

## General Guidance

**Human safety must be the top priority. Aircraft can be replaced. People cannot. Always prioritize the safety of yourself and others over the preservation of aircraft or equipment.**

Emergency situations are dynamic events, that will not often conform perfectly to the categories listed below. A thorough understanding of aircraft systems, proficiency in piloting the aircraft, and sound judgment will allow you to bring about the best possible outcome in an emergency.

The likelihood of an emergency can be reduced substantially through [proper aircraft maintenance](/broken/pages/-MfEfk7y0P474WN5vrmM), the use of [checklists for normal procedures](/broken/pages/-MfEfCAXYq5xABmbFcTc#checklists), and careful pre-flight planning. The likelihood of a safe flight often depends on the diligence of the pilot, both before taking off and during operation.

In general, if an emergency occurs, three basic actions can be applied to most situations:

1. Maintain aircraft control — Small emergencies can quickly escalate if the pilot is distracted attempting to troubleshoot the problem. Always maintain visual contact with the aircraft during an emergency to reduce the likelihood of losing orientation.
2. Analyze the situation — Once the aircraft is stabilized, assess the cause of the emergency.
3. Take appropriate action — In many cases, the appropriate action will be to land the aircraft as soon as possible. Aircraft can be replaced.&#x20;

### Return Mode

Do not be over-reliant on [Return Mode](operation.md#return) in emergency situations. The cause of the emergency may degrade performance or disable Return Mode. For example, loss of GPS disables Return Mode.

{% hint style="warning" %}
Depending on what Astro firmware version you're on, you may or may not be able to move sticks to interrupt Return Mode&#x20;

Before Astro version 1.4.6, moving the flight sticks on the controller will interrupt Return and Mission mode.&#x20;

For Astro version 1.4.6-1.5.18, moving the flight sticks will not interrupt these modes.&#x20;

In 1.6.14 and later this setting was re-introduced as an opt-in setting that's disabled by default, and by default stick movements will not interrupt Return Mode

This change was made as a response to feedback that accidental stick movements were interrupting these flight modes erroneously. To change this behavior, you can toggle [Advanced Mode](https://freefly.gitbook.io/astro-public/astro/pilots-operating-handbook/software/auterion-mission-control/amc-vehicle-setup/advanced-vehicle-setup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) and change the COM\_RC\_OVERRIDE parameter to 1 in Vehicle Setup.
{% endhint %}

## Emergency Procedure Checklists

The [Astro checklists](https://freefly.gitbook.io/astro-public/products/astro/pilots-operating-handbook/flight#checklists) contain concise instructions to follow to mitigate risk in the event of an in-flight emergency. Some of these situations are discussed in more detail below.

{% tabs %}
{% tab title="Orientation Loss" %}
### Loss of Orientation

If orientation is lost, neutralize inputs and activate position mode. Then work to identify the front of the aircraft.

We recommend identifying the front of the aircraft via a "guess and check" method of small roll right inputs alternating with yawing the aircraft 90 degrees at a time. We recommend a roll input rather than pitch because at a distance it is easier to see lateral motion than fore/aft motion.

If it is not possible to identify orientation, and it is safe to activate Return Mode, do so. By default in Return Mode, after climbing, the aircraft will yaw to put the front toward the direction of flight.

Resume flying or land as necessary.
{% endtab %}

{% tab title="Unexpected Behavior" %}
### Unexpected Aircraft Behavior

If Astro behaves unexpectedly, do the following: neutralize inputs, activate Position Mode, and observe the aircraft. If it is still flying in an uncommanded manner in Position or Altitude Mode, switch to Manual Mode.&#x20;

In some cases, unexpected behavior is due to degraded GPS signal or erroneous sensor readings (e.g. compass error). In such cases, Return Mode may not behave reliably. Manual Mode does not rely on these sensors.

Land as soon as possible.
{% endtab %}

{% tab title="Landing Detector Failure" %}
### Landing Detector Failure

If the aircraft touches down, but hops back up into the air several times, or sits on the ground with the props continuing to spin, the autopilot may not have detected a landing. Climb and retry landing with a greater downward velocity.

{% hint style="info" %}
Landing the aircraft firmly will give the accelerometers and gyroscopes a sufficient contrast between flight and landing.
{% endhint %}

If an attempted landing is unsuccessful in Position and Altitude mode, land in Manual Mode.

If an attempted landing is unsuccessful in Manual Mode, perform an [Emergency Stop](operation.md#emergency-stop) with the aircraft on the ground or as close as possible.
{% endtab %}

{% tab title="GPS Loss" %}
### Loss of GPS

If GPS is lost, flight modes that rely on GPS (Position, Return, Mission, etc) will not be available. If the aircraft is in Position mode when GPS is lost, the autopilot will switch to Altitude Mode. If the aircraft is in Return or Mission modes when GPS is lost, it will automatically start landing. Landing can be overridden by the pilot by changing modes to Altitude or Manual modes.

{% hint style="info" %}
It is the pilot's responsibility to be proficient with Altitude and Manual Mode and to have the aircraft configured to behave safely if GPS is lost.
{% endhint %}

Examples of behavior without GPS:

* If GPS is not available upon arming, no Home Point is set, and Return Mode is not available. Even if GPS becomes available while flying, Return Mode will not be available.
* If the pilot commands Return Mode, the aircraft will remain in Altitude or Manual Mode, and an error will be displayed on the pilot handset.
* If Land Mode is activated (e.g. by a failsafe), the aircraft will descend as though in Altitude mode, maintaining a consistent descent but drifting with the wind.
* If GPS is lost in Position, the aircraft will display a warning and switch flight mode to either Altitude Mode or Manual Mode, depending on the degradation of the signal and other sensors
* If GPS is providing altitude information (e.g. while using RTK GPS), and GPS is lost, the ability of Altitude Mode to accurately maintain altitude may be affected.
{% endtab %}

{% tab title="RC Loss of Signal (LOS)" %}
### RC Loss of Signal (LOS)

RC Loss of Signal (LOS) can occur if the pilot handset signal is degraded or stops, or if Astro does not receive the signal due to distance or interference (e.g. from obstacles or other radio signals).

If the signal is lost longer than the RC Timeout, a failsafe action will be triggered. The RC Timeout is quite short by default: 0.5 seconds. The pilot may not have time to react before the failsafe action is activated. By default, the failsafe action is Return Mode.

If the signal is lost, check the pilot's handset power and [antenna orientation](../other-user-manuals/ecosystem/components/pilot-handsets/#antennas). Antenna orientation is especially important when Astro is far from the pilot.

If the signal is recovered, the pilot will be able to take control via moving the sticks or pressing a flight mode button.

{% hint style="info" %}
RC Loss of Signal (LOS) is differentiated from Data Link Loss. LOS refers to the stream of SBUS data containing the pilot's inputs. Data Link refers to the stream of MavLINK messages. Astro routes both data streams through a single radio system. Please note that the AMC app needs to be in the foreground on the pilot handset during operation; Data Link will fail after 30 seconds and trigger a failsafe if the AMC app is closed or running in the background.&#x20;
{% endhint %}
{% endtab %}

{% tab title="Video Loss" %}
### Loss of Video Signal

Loss of Video Signal can occur if the aircraft flies out of range or if it flies behind an object that interrupts the signal. Maintaining visual contact is the preferred method to re-establish control of the aircraft, either with the pilot seeing the aircraft or by the use of a visual observer.

Yawing the aircraft can help signal reception if the body of the aircraft is blocking the line of sight between the transmitter and receiver antennas.

If video signal or visual contact cannot be re-established, enable Return Mode to bring the aircraft back to signal reception range.

{% hint style="danger" %}
It is the responsibility of the pilot to see and avoid other aircraft, people, or obstacles. Always maintain a direct line of sight with Astro during flight, use visual observers as operations require, and follow local regulations regarding see-and-avoid requirements.
{% endhint %}
{% endtab %}
{% endtabs %}

## Emergency Stop

{% hint style="danger" %}
#### As a last resort, if it is not possible to land or control the aircraft, perform an Emergency Stop. If performed while flying, this will cause the aircraft to crash. Perform the Emergency Stop as far away from people as possible.
{% endhint %}

{% tabs %}
{% tab title="AMC" %}
### Emergency Stop - AMC

In AMC on the pilot handset or PC, tap the "Armed" button at the top center of the screen to display the Emergency Stop dialogue. Hold the Emergency Stop button for 4 seconds. This works on the pilot handset or PC.

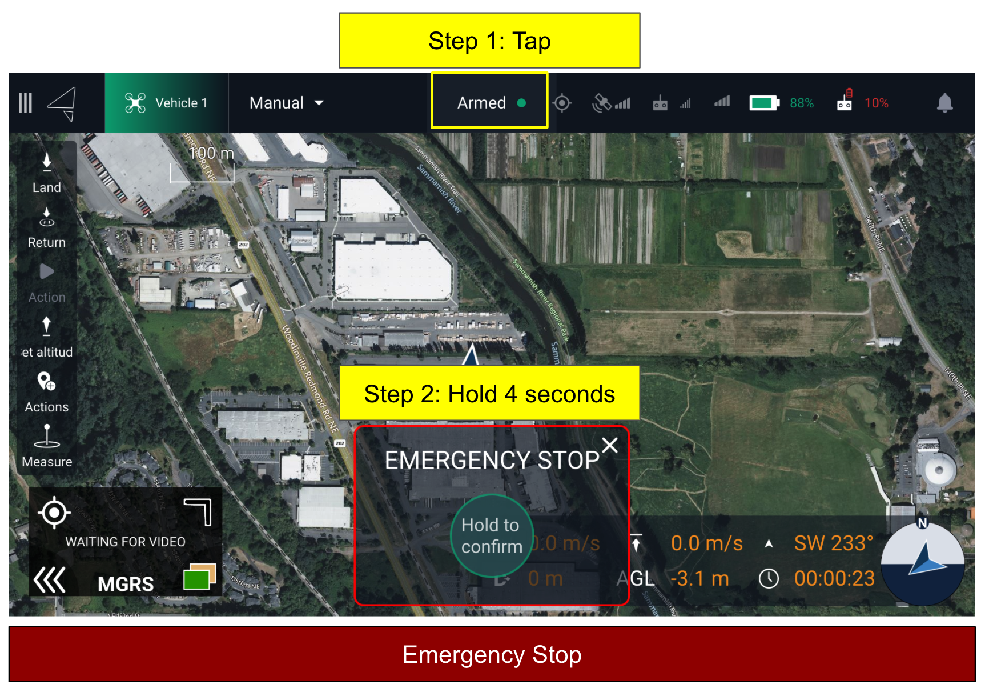
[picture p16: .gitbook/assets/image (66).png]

{% endtab %}

{% tab title="Manual Override" %}
### Emergency Stop - Manual Override

In Manual Mode, hold the throttle stick down and left for 10 seconds.

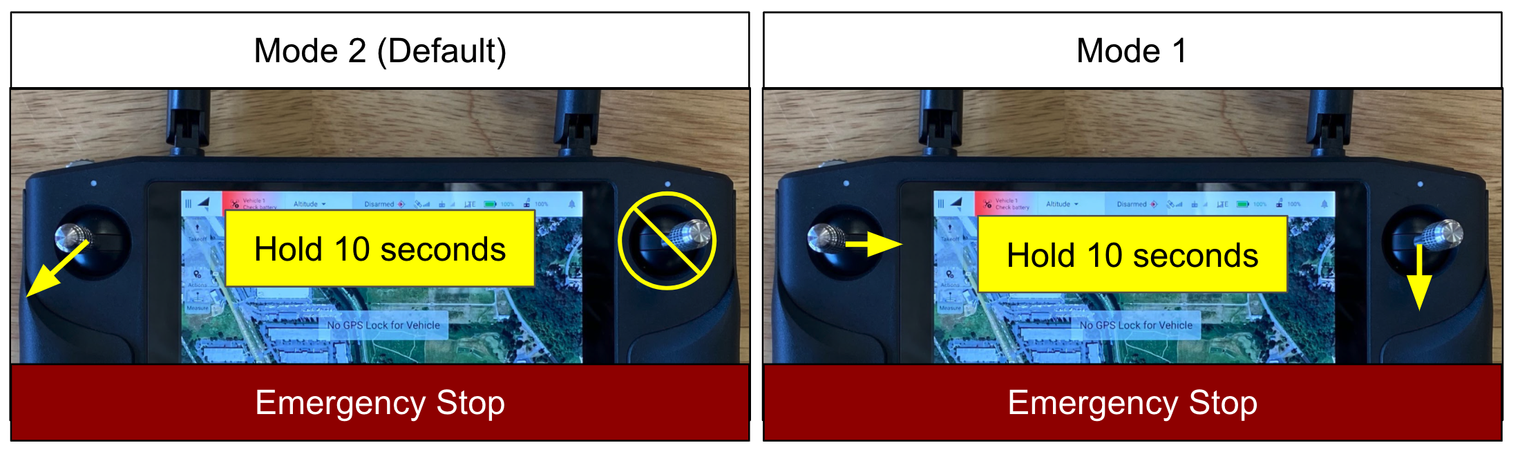
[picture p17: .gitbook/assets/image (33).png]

{% endtab %}
{% endtabs %}

## Failsafes

Failsafe behavior and settings are configured in AMC. The [AMC documentation ](https://docs.auterion.com/vehicle-operation/settings-and-maintenance/safety)covers each failsafe and related settings in detail.

Some failsafes are discussed briefly below.

{% hint style="warning" %}
We strongly recommend using the default settings, changing only Return Altitude, unless you are an expert user and have tested the effect of changes thoroughly.
{% endhint %}

{% tabs %}
{% tab title="Low Battery" %}
### Low Battery

Battery level is evaluated from the State of Charge (SoC, e.g. 72%), not voltage (e.g. 23 Volts).

As the battery level becomes low, the autopilot can take action. The default settings do not interfere until the battery becomes quite low. Additionally, low battery failsafes are only able to estimate how long it will take the aircraft to return to the home point. This means it is the pilot's responsibility to be aware of the battery level and ensure the aircraft is on the ground.

<table><thead><tr><th width="257.3333333333333">State</th><th>SoC (default)</th><th>Action (default)</th></tr></thead><tbody><tr><td>Warning</td><td>20%</td><td>Warning: Flash boom LEDs</td></tr><tr><td>Critical (>200m)</td><td>17-15%</td><td>Return Mode</td></tr><tr><td>Critical (&#x3C;200m)</td><td>10%</td><td>Return Mode</td></tr><tr><td>Emergency</td><td>6%</td><td>Land Mode</td></tr></tbody></table>

{% hint style="info" %}
When activated by a low battery failsafe, Return and Land Mode cannot be overridden by stick movement. They can be overridden by pressing a flight mode button (e.g. Position).
{% endhint %}
{% endtab %}
{% endtabs %}

## Error and Warning Indication&#x20;

The aircraft communicates the presence of errors and warnings primarily through Auterion Mission Control (AMC) [status indicators](https://docs.auterion.com/auterion-mission-control/fly/fly-view-ui-overview#vehicle-status-indicators-top-bar) on the pilot handset or PC. Many messages are accompanied by an audible message (e.g. "Return Flight Mode"). Additionally, Astro boom LEDs will flash when the battery level is low.&#x20;

Status messages, including errors and warnings, are stored in Flight Logs. After any emergency, review the log to determine the source of the problem.

If the meaning of an error or warning is not clear, please [contact Freefly Support](https://freeflysystems.com/support/astro-support). Share as much detail as possible, including [sharing the flight log](essential-software/auterion-suite.md#flight-logs).

## Advanced Arming Methods

| Method | Input |
| --- | --- |
| AMC App, pilot handset | Tap the Arm button (top center) and hold to confirm. |
| Mission | If a mission starts with the takeoff command, and the aircraft is disarmed, the aircraft will arm itself when the mission is initiated. |

{% hint style="info" %}
Arming via the AMC app in Manual Mode is not recommended. In Manual Mode, the aircraft should be armed while the throttle stick is held at the minimum position. This is difficult to achieve while using an app GUI.
{% endhint %}

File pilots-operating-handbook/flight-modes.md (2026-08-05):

---
icon: drone-front
---

# Flight Part 1 - Flight Modes

### Flight Modes

{% embed url="https://www.youtube.com/watch?v=vJHQdul398g" %}

{% hint style="info" %}
Note that this video features the legacy Herelink controller with the original Astro. However, the flight modes and their behavior are unchanged unless otherwise noted in this guide.&#x20;
{% endhint %}

Astro offers several flight modes with varying levels of assistance to the pilot.

Flight mode can be changed via the buttons on the Pilot Pro/Herelink or the AMC app on the handset/PC. See the documentation for the equipment you're using to become familiar with the buttons/switches involved.

{% tabs %}
{% tab title="Pilot Pro" %}
<figure><figcaption><p>Manual mode switch buttons on the Pilot Pro controller</p></figcaption></figure>
{% endtab %}

{% tab title="Herelink Controller" %}
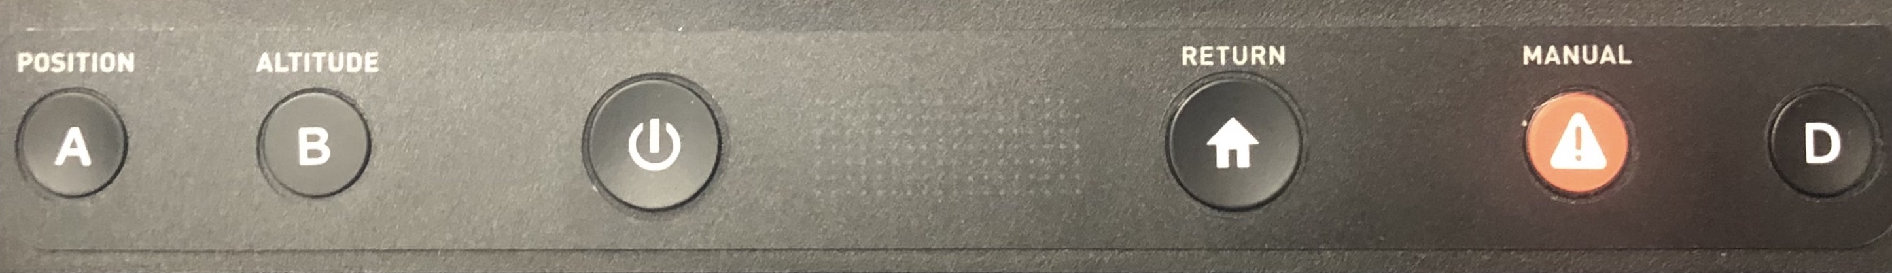
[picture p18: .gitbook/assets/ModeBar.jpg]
<figure><figcaption><p>Manual mode switch buttons along the bottom of the Herelink controller.</p></figcaption></figure>
{% endtab %}
{% endtabs %}

{% hint style="success" %}
Manual Mode may be necessary to react to emergency situations. Pilots should be proficient in Manual Mode. Position, Altitude, and Return Mode are assistive only and are not a replacement for pilot skill and preparedness.&#x20;
{% endhint %}

{% hint style="warning" %}
Always neutralize the control input sticks on the pilot handset when switching between control modes to prevent unexpected aircraft movement.
{% endhint %}

### Pilot-controlled Modes

{% tabs %}
{% tab title="Position" %}
<figure><figcaption><p>Position Mode Button on Pilot Pro</p></figcaption></figure>

In Position Mode, when the sticks are centered, the aircraft will maintain its position over a point on the ground and maintain altitude, correcting for disturbances.

In Position Mode, the pitch/roll stick commands the speed of the drone relative to the ground. The further upward the pitch/roll stick, the faster Astro will fly forward. When the pitch/roll stick is pulled downward, Astro will fly backward. Similarly, the pitch/roll stick will move the drone in the left and right directions when moved to the left and right.

The throttle stick commands vertical speed. The further upward the throttle stick, the faster Astro will climb. Conversely, the lower the throttle stick position, the faster Astro will descend. Deflecting the throttle stick left and right controls the yaw rate, with the speed of rotation proportional to stick deflection.

{% hint style="info" %}
Position Mode requires a strong GPS signal. If a weak signal is present, Astro will not enter Position Mode.&#x20;

If the signal deteriorates, such as near buildings or under dense tree cover, the aircraft will automatically revert to Altitude mode.
{% endhint %}

{% hint style="danger" %}
Flight using Position Mode in areas of degraded GPS signal, such as near buildings or under dense tree cover, is not recommended. The automatic reversion to Altitude Mode can cause unexpected, abrupt changes in flight behavior.
{% endhint %}
{% endtab %}

{% tab title="Altitude" %}
<figure><figcaption><p>Altitude Mode Button on Pilot Pro</p></figcaption></figure>

Similar to Position mode, the pitch/roll stick moves Astro laterally relative to the ground and the throttle stick commands vertical speed and yaw. However, while the drone can hold its vertical position using the barometer, lateral speed is not controlled by the autopilot in Altitude mode. Astro will drift with the wind, will not stop immediately after lateral movement, and will probably not hold a single point above the ground without pilot input.&#x20;

{% hint style="info" %}
The aircraft holds altitude above Mean Sea Level (MSL) by default. It is not aware of terrain height changes or obstacles without additional configuration and equipment.
{% endhint %}
{% endtab %}

{% tab title="Manual" %}
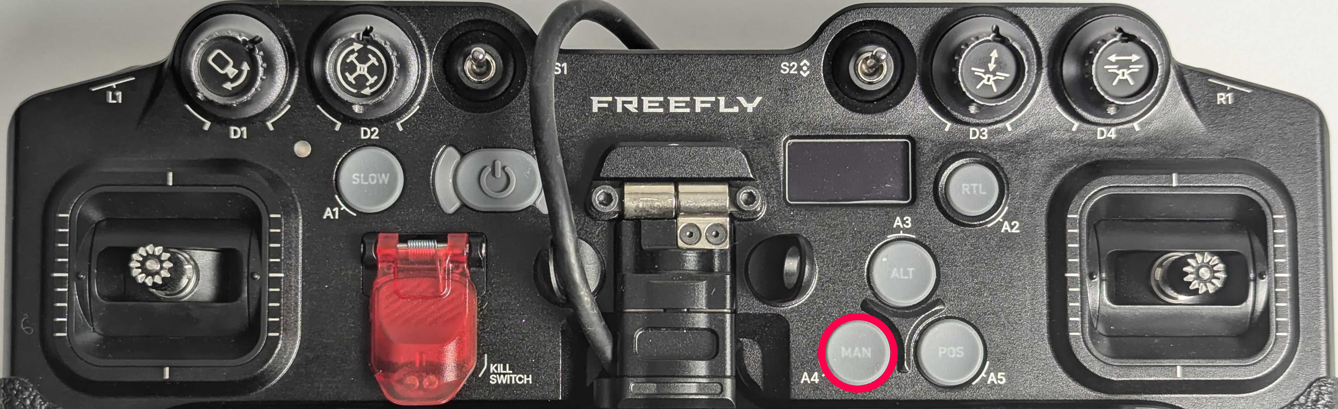
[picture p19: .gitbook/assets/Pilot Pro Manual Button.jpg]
<figure><figcaption><p>Manual Mode Button on Pilot Pro</p></figcaption></figure>

In Manual Mode, when the pitch and roll stick is centered, the aircraft will attempt to remain level and will drift with the wind. The aircraft will require constant throttle adjustment to hold altitude.

In Manual Mode, the pitch and roll stick controls the aircraft angle. The further upward the pitch stick, the further Astro will tilt forward. When the pitch stick is pulled downward, Astro will tilt backward. Similarly for roll in the left and right directions. Lateral speed is not controlled by the autopilot.

The throttle stick controls motor speed directly. Deflecting the throttle stick left and right controls the yaw rate. The speed of yaw rotation is proportional to stick deflection.

#### Manual Mode Settings

The hover throttle setting controls the amount of thrust Astro produces when the throttle stick is centered. The default setting of 34% will hover the aircraft with no payload. A setting of approximately 40% will hover with 1500 grams of payload.&#x20;

Adjust this setting in AMC on the pilot handset or PC:

1. Enable [Advanced Mode ](https://freefly.gitbook.io/astro-public/pilots-operating-handbook/essential-software/auterion-mission-control/amc-vehicle-setup/advanced-vehicle-setup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)
2. Vehicle Setup > Tuning<br>

#### Learn Manual Mode

{% embed url="https://www.youtube.com/watch?v=3eNAD1Ip-9s" %}
{% endtab %}

{% tab title="Position Slow" %}
<figure><figcaption><p>Position Slow Mode Button on Pilot Pro</p></figcaption></figure>

Position Slow acts just like regular Position Mode, but helps to give your flying more control over speed of movement. With the dials on the top of the Pilot Pro, you can now adjust velocity rates on the fly! Whether flying for tower inspections or a cinematic sweep, Position Slow helps give finesse to the pilot to achieve this with ease.&#x20;

{% hint style="info" %}
The gimbal's dial on the left is always active regardless of mode
{% endhint %}

{% hint style="warning" %}
Position Slow was added in Astro v1.4.6 when the Pilot Pro was introduced and has not been tested on the Herelink controller. While it may be accessible depending on software version, you will not have options to change speeds dynamically that you do on the Pilot Pro. To map Position Slow to the D button, open AMC and under Advanced > Flight Modes, set Flight Mode 5 to Position (Slow). Next, enter the Herelink settings by swiping down from the top of the screen and clicking the Herelink stats. Go to the "BUTTONS" tab and change "D short press" from channel 10 to 14, then hit save.
{% endhint %}
{% endtab %}
{% endtabs %}

### Autonomous Modes

{% tabs %}
{% tab title="Return" %}
<figure><figcaption><p>Return Mode Button on Pilot Pro</p></figcaption></figure>

Return Mode commands Astro to climb to the Return Altitude, fly back to the Home Point in a straight line, and land. Return Mode requires GPS.

Return Altitude is set by the pilot at AMC > Vehicle Setup > Safety. Please note that if Astro is above the Return Altitude when Return Mode is initiated, it will maintain altitude instead of dropping to the return altitude.&#x20;

The Home Point is set to the GPS coordinates where Astro is armed. Home Point is reset every time Astro is armed.

By default, Return Mode is activated automatically by some Failsafes.

{% hint style="warning" %}
Before every flight, think through the path the aircraft will take if Return Mode is activated, and adjust settings to arrange for safe behavior.

For example, activating Return Mode while flying under an obstacle lower than the Return Altitude will cause a collision when the aircraft attempts to climb to Return Altitude. In some cases, it may be possible to set a lower Return Altitude, and in other cases, it may not be possible to use Return Mode.
{% endhint %}

{% hint style="info" %}
It is possible to change from Return to Position Mode by moving the sticks, except if Return Mode was activated by the low battery failsafe. In that case, press another flight mode button to change out of Return Mode.
{% endhint %}

In most cases, RTL mode will travel to the predetermined RTL altitude, travel over the home point, and automatically descend to land. However, if the aircraft is close to the home point, the behavior will be slightly different in order to save time and reduce the amount of distance Astro will need to move.

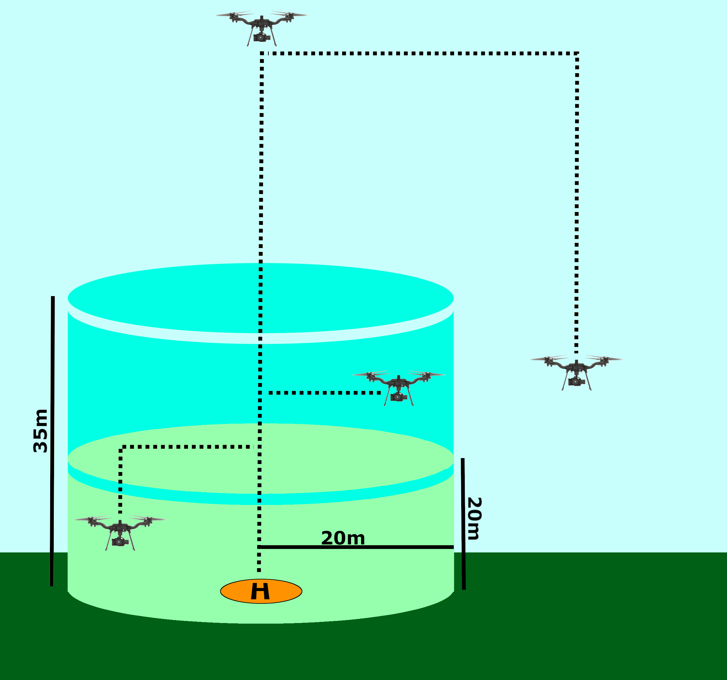
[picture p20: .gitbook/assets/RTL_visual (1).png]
<figure><figcaption></figcaption></figure>

* If Astro is directly over the home point at the time of RTL, it will land without gaining altitude regardless of its current altitude.&#x20;
* If Astro is within a few meters of the home point, it will move directly above the home point and begin landing.
* If Astro is within 20m altitude and less than 20m ground distance from the home point, it will go to 20m altitude, move over the home point, and land.
* If Astro is between 20-35m altitude and less than 20m ground distance from the home point, it will maintain altitude, move over home point, and land.
* If Astro is more than 35m altitude or more than 20m ground distance from the home point, it will go to the set RTL altitude, move over the home point, and land.

&#x20;
{% endtab %}

{% tab title="Takeoff" %}
Takeoff Mode arms the aircraft, automatically climbs to the Takeoff Altitude, and enters [Hold Mode](https://docs.px4.io/v1.12/en/flight_modes/hold.html) (a.k.a. loiter or hover).

Takeoff Mode can be engaged via the button in the AMC app Fly view, optionally changing Takeoff Altitude via the slider, then holding/sliding to confirm. Takeoff Mode can also be engaged during a mission, for example as the first command.

{% hint style="info" %}
Takeoff Mode requires a GPS lock.
{% endhint %}

{% hint style="info" %}
Moving the sticks while in Hold Mode (i.e. after the aircraft has finished climbing) will cause a change to Position Mode. This makes it easy to take control without pressing the Position Mode button.
{% endhint %}
{% endtab %}

{% tab title="Landing" %}
### Landing Mode

Landing Mode causes Astro to descend and land directly below the position where Land Mode is engaged. Once on the ground, Astro will disarm.

Landing mode can be engaged via the button on the AMC app Fly screen. You'll need to hold the button down to confirm the switch.&#x20;

Landing Mode is often the last command in a mission. It can also be engaged by a failsafe, such as low battery level, or loss of signal.

{% hint style="info" %}
Land Mode requires GPS when engaged manually.&#x20;

When Land Mode is engaged by a failsafe, and GPS is not available, the autopilot behavior will be similar to Altitude Mode and the aircraft may drift horizontally as it descends.
{% endhint %}

{% hint style="info" %}
Moving the sticks will cause a change to Position Mode unless Landing Mode is engaged by a Failsafe (e.g. critical battery level). See the [Safety and Failsafes section](/broken/pages/-LaNWMwiqb_UzRIMSvUW) for more details.

When activated by a low battery failsafe, Return and Landing Mode cannot be overridden by stick movement. They can be overridden by pressing a flight mode button (e.g. Position).
{% endhint %}
{% endtab %}

{% tab title="Mission" %}
Mission Mode allows Astro to execute a predefined autonomous waypoint mission that has been uploaded to the flight controller via AMC. For more information on all the different options and abilities built into the Mission Mode, see the AMC docs, sections such as:

* [Planning a mission](https://freefly.gitbook.io/astro-public/astro/pilots-operating-handbook/software/auterion-mission-control/amc-plan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)
* [Flying a mission](https://docs.auterion.com/auterion-mission-control/fly/flying-a-mission)
* [Remove a mission from the aircraft](https://docs.auterion.com/auterion-mission-control/plan/plan-ui-overview#file-sync-tools)

{% hint style="danger" %}
Starting a mission can cause the aircraft to arm itself and take off without any further pilot input. Before starting a mission, ensure that the aircraft is clear of obstacles in the propeller arc and flight path.
{% endhint %}

If a mission is interrupted (for example, by the pilot switching to Position mode), the Fly view will prompt to resume the mission. If a prompt is not shown, open the [Action Menu](https://docs.auterion.com/auterion-mission-control/fly/fly-view-ui-overview#fly-tools) and select "Resume Mission".

{% hint style="warning" %}
Astro must have a GPS lock before takeoff to set a valid home position to start a mission. Mission mode will be unavailable if the aircraft takes off before a GPS lock is achieved. The pilot must land and rearm with a GPS lock to enable it.
{% endhint %}

{% hint style="warning" %}
Depending on what Astro firmware version you're on, you may or may not be able to move sticks to interrupt Return Mode&#x20;

Before Astro version 1.4.6, moving the flight sticks on the controller will interrupt Return and Mission mode.&#x20;

For Astro version 1.4.6-1.5.18, moving the flight sticks will not interrupt these modes.&#x20;

In 1.6.14 and later this setting was re-introduced as an op-in setting that's disabled by default, and by default stick movements will not interrupt Return Mode

To change this behavior, you can toggle [Advanced Mode](https://freefly.gitbook.io/astro-public/astro/pilots-operating-handbook/software/auterion-mission-control/amc-vehicle-setup/advanced-vehicle-setup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) and change the COM\_RC\_OVERRIDE parameter to 1 in Vehicle Setup.&#x20;

These changes were made as a response to feedback that accidental stick movements were interrupting these flight modes erroneously along with a userbase that wanted this behavior back.&#x20;
{% endhint %}
{% endtab %}
{% endtabs %}

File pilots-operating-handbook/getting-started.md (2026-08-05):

---
description: How to get set up for a successful and safe first flight!
icon: keyboard-brightness
layout:
  width: default
  title:
    visible: true
  description:
    visible: true
  tableOfContents:
    visible: true
  outline:
    visible: true
  pagination:
    visible: true
  metadata:
    visible: true
  tags:
    visible: true
  actions:
    visible: true
---

# Getting Started

{% stepper %}
{% step %}
### Unboxing and Powering Your Astro

Open up the Astro case and you will see the Astro, a quick start guide, and the controller.

Remove the[ Pilot Pro controller](https://docs.freeflysystems.com/ecosystem/controller/pilot-pro) from the case, peel off the sticker from the controller screen, and press the power button twice to power it on. The Pilot Pro app will automatically open.

Pull the Astro out of the case, and set it down on a hard, stable surface.

Align one [SL8 battery](https://docs.freeflysystems.com/ecosystem/power/superlight-batteries) onto the Astro, and slide it into place with enough pressure to hear two clicks. This means that the battery is electrically connected to the Astro.

If you have a [compatible payload](https://docs.freeflysystems.com/ecosystem/payloads/payloads-overview#freefly-payloads), such as the [Sony LR1](https://docs.freeflysystems.com/ecosystem/payloads/lr1-payload), you should [connect your payload](https://docs.freeflysystems.com/ecosystem/payloads/payload-maintenance/installing-removing-payloads) before powering on the Astro.

{% hint style="danger" %}
The Smart Dovetail is not designed for hot-swapping payloads. Ensure that the Astro is powered off when connecting or removing payloads.
{% endhint %}

Once your payload is connected and secured, press the button on the battery once to wake the battery, then again to send power to the Astro.

{% hint style="warning" %}
Powering Astro with only 1 battery will prevent arming, making it much safer to have powered on while the propellers are installed. This is not a substitute for the absolute safety of removing propellers.
{% endhint %}
{% endstep %}

{% step %}
### Getting Hardware Charged and Ready

You should have received batteries in a separate shipment. The chargers for these batteries are going to be located in the Astro case, under the battery foam insert.

Connect the Astro batteries to the chargers and charge until complete.

Using the included 65W charger, plug in the Pilot Pro controller using the left-most USB-C port, and charge until complete.

Finally, ensure that your Astro [firmware is up to date](https://docs.freeflysystems.com/astro/maintenance/software-release-notes/software), and Pilot Pro has the [latest updates](https://app.gitbook.com/s/WXREyAKYAeQJ4gfg2SPg/controller/pilot-pro/maintenance/software-and-firmware-updates).

{% endstep %}

{% step %}
### Learn How to Operate Astro

While your batteries and controller charge, read the [Flight section of this wiki](operation.md), and learn how to control Astro.

If you are getting started with the **NDAA/Blue** version of the Astro, make sure to read the Doodle radio notes in our [Pilot Pro docs](https://app.gitbook.com/s/WXREyAKYAeQJ4gfg2SPg/controller/pilot-pro/operating-handbook/radio-modules/doodle-labs-radio-module), as well as the different configurations and parameters in [DIU Blue sUAS](../other-user-manuals/compliance/diu-blue-suas.md).

Learn about common workflows like [Photogrammetry Mapping](https://docs.freeflysystems.com/ecosystem/workflows/photogrammetry-mapping) and [LiDAR Mapping](https://docs.freeflysystems.com/ecosystem/workflows/lidar-mapping). Visit our [workflows page](https://app.gitbook.com/s/WXREyAKYAeQJ4gfg2SPg/workflows) for all our guides on how to put Astro to work.&#x20;

Check out the [Freefly Astro Training Playlist](https://www.youtube.com/playlist?list=PLlKTld1e-W1wUvac10cbtM5Aru1su0QOO) on YouTube for some visual instruction.

{% hint style="warning" %}
Pilot skill with [Manual Mode](flight-modes.md#manual) is required for[ Emergency Procedures](emergency-procedures.md#emergency-procedure-checklists).&#x20;
{% endhint %}
{% endstep %}

{% step %}
### Go Flying!

To ensure that the Pilot is using best practices, there is a quick checklist card included in the Astro case. The digital version is found in[ Part 2 - Operation](operation.md#astro-flight-checklist).

Freefly also offers [official Astro Training](https://store.freeflysystems.com/collections/astro/products/astro-training) for up to 5 students at a time!&#x20;

If you'd like to review the [flight logs](https://docs.freeflysystems.com/ecosystem/software/flight-logs), you can download and analyze them any time.

Now that you have completed your first flight, dive in, learn the details, and put Astro to work!
{% endstep %}
{% endstepper %}

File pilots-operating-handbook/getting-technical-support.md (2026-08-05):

---
icon: comment-question
---

# Getting Technical Support

Freefly prides itself in providing the best technical support in the industry. You can send us a message any time, and our staff will get back to you as soon as possible.&#x20;

Our office hours are Mon-Fri, 8am - 4pm PST.&#x20;

### How to get in touch

1. Use our [contact page](https://freeflysystems.com/contact) (preferred)
2. Send an email directly to [support@freeflysystems.com](emailto:support@freeflysystems.com)
3. While you wait for a response, try using the AI search below for a quick answer to your questions that can be found on this guide. Since this is an aircraft, always be sure to verify information. <br>

{% hint style="info" %}
AI can make mistakes. If you're not sure, just contact us directly to verify information.&#x20;

Freefly is not liable for any mistakes that the AI generates for you.
{% endhint %}

<button type="button" class="button primary" data-action="ask" data-icon="sparkles">Ask a question…</button>

### Getting your issues resolved faster

When you reach out to our support team, there are a few things that are commonly going to be asked. To reduce the time it takes to get to a solution, it's best to provide as much detail as possible, including:

1. Your aircraft's serial number. For Astro, this will be found on the bottom chassis. \
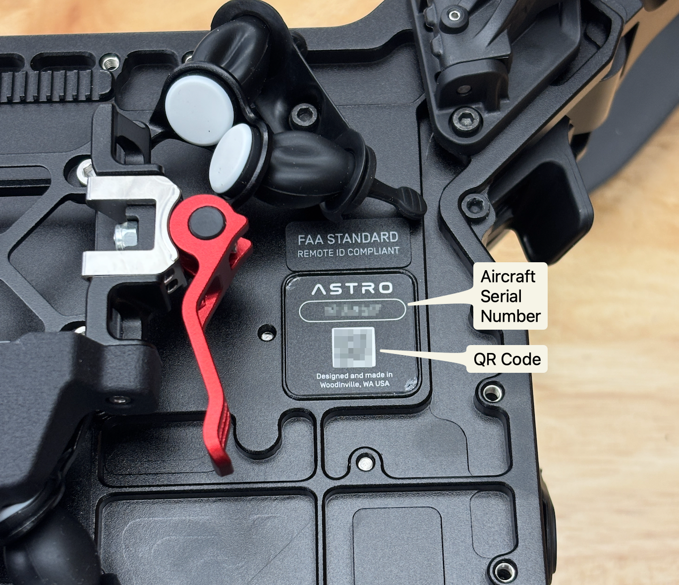
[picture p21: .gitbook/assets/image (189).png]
   
2. Any photos and/or videos that can clearly demonstrate the issue.
3. Flight logs, even if the issue(s) took place on the ground. [How to send logs](https://app.gitbook.com/s/WXREyAKYAeQJ4gfg2SPg/software/flight-logs).
4. Any other relevant information, including current firmware version, pilot statements, etc.

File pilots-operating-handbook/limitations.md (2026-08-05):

---
icon: lightbulb
---

# Pro Tips and Limitations

It is possible to operate Astro close to the limits of performance by maintaining awareness of the performance envelope, how the aircraft behaves if the limits are exceeded, and best practices for operating in harsh environments.

This page reflects the limitations of the most current version. As the Astro platform matures, limitations are likely to change. For major changes that may affect these limitations, check the [release notes](https://freefly.gitbook.io/astro-public/products/astro/maintenance-manual/software-release-notes).

***

## Troubleshooting

Visit our [Troubleshooting Spreadsheet](https://docs.google.com/spreadsheets/d/1DXkk0BmRx9qLbjpBt2KgKYFOQhEGUTcyyQB6rOmb4ac/edit#gid=528435697) to look into additional solutions if you aren't finding what you're looking for on the wiki.&#x20;

***

## Flight Control

For all flight modes except Manual, at altitudes below 2 meters, the tilt angle is reduced to 12 degrees and vertical speed is reduced to 0.7 m/s.

The purpose is to prevent tip-overs while landing but has the side effect of reducing speed if flying below the takeoff point (e.g. surveying from a high vantage point). We are working to correct this behavior.

***

## Continuous Operation

With eight (8) SL8 batteries, six (6) SL8 chargers, and access to power at your flight location, you can keep Astro in continuous operation. Two batteries fly the aircraft while the remaining six charge, so a freshly charged set is always ready when you land. Swap the packs, take off again, and put the depleted set back on the chargers.

{% hint style="warning" %}
In hot conditions, you will likely need an additional two batteries, as it may take some time to cool the recently flown batteries to an acceptable charging temperature (below 50°C).&#x20;
{% endhint %}

For more information on batteries, click the page link below.

{% content-ref url="../other-user-manuals/ecosystem/components/batteries.md" %}
[batteries.md](../other-user-manuals/ecosystem/components/batteries.md)
{% endcontent-ref %}

***

## Radio Range and Interferences

Operating with a weak signal, whether due to interference or long range, can cause loss of link with the aircraft, which will engage failsafes. If you anticipate a weak signal situation, double-check that failsafes are set appropriately.

### Range

The range of Herelink and the Doodle radios on Astro is approximately 2 km in ideal conditions, assuming there are no interferences and the antennas are positioned correctly.

### Antenna Positioning

{% hint style="warning" %}
This is one of the simplest to miss and impact the range of the flight
{% endhint %}

#### **Pilot Pro**

Both the Doodle and Herelink radio modules on Pilot Pro use two blade antennas that are omni directional. It is important to follow these basic guidelines:

* Antennas should both point in the same direction.&#x20;
* Antennas should point towards ground for best signal quality in most situations.

<figure><figcaption></figcaption></figure>

#### **Herelink GCS (Legacy):**&#x20;

Herelink GCS has two types of antennas.&#x20;

* Patch antenna (with a circular disk on top) is a directional antenna and should be pointed toward the aircraft
* Other antenna is omni-directional and it should be positioned pointing towards the ground or sky

### Interferences

Usable range depends heavily on the RF environment. Radio interference from nearby transmitters operating in the same frequency band, such as WiFi access points, can reduce both range and link quality. Physical obstructions affect the signal as well, such as trees, buildings, and terrain near the controller, near the aircraft, or directly in the line of sight between them can reduce range\
significantly.

### Multiple Aircraft

* Astro's Doodle radio configuration runs on dedicated peer to peer channels. In order to fly multiple Astros in the same airspace, make sure to scan channels and then set each Astro Doodle to a different channel.
* Astro's Herelink radios are channel hopping by default. 4 aircraft can fly simultaneously in the same airspace in practice. If more aircraft are present, interference can cause loss of radio link and control.
  * If using the legacy Herelink GCS, you can set each Herelink to be on a dedicated channel
  * If using the Pilot Pro with the Herelink radio, this feature is not yet available.

### High Power Radio Interference

Avoid using high-power, low-frequency radio transmitters (such as the RFD 900) mounted to Astro, as it can disrupt the normal function of the aircraft. For more information,  see this [service bulletin](https://freeflysystems.com/knowledge-base/astro-sb002-high-power-radio-astro-interference).&#x20;

***

## Environment

### Temperature



Astro can operate between -20 and 50 C. Position mode and survey flying are normal throughout the range. However, care is needed to operate at low and high temperatures.

Yellow region: Hovering and aggressive flights may give overtemp warnings. Follow the warning instructions.

Blue region: If batteries become too cold, state of charge will decline quickly and aircraft will enter Return or Land mode. Keep batteries warm, above 10 °C at takeoff, then self-heating will keep them warm.&#x20;

{% tabs %}
{% tab title="Tips for operating in hot environments" %}
At high temperatures, the limiting factors are motor and battery temperatures. AMC will display a warning if the motors or batteries become too hot. Heed the warnings! Astro operates normally in forward flight up to 15 m/s with a full payload of 1500 grams.&#x20;

Cooling air is your friend. The motors get much more cooling air in forward flight than in a hover. Overheat errors may occur when hovering because there is less airflow, or when flying aggressively because heating increases with current.

Batteries may require cooling before charging. Bring an extra set of batteries and chargers to enable continuous flying. If you connect batteries to the charger while cooling, they will automatically begin charging as soon as they have cooled sufficiently.
{% endtab %}

{% tab title="Tips for operating in cold environments" %}
At low temperatures, the battery cell temperature is the key limiting factor. When the cells themselves are below 10 °C (ambient air can be down to -20 °C), the built-in battery management system's (BMS) state of charge (SoC) algorithm has reduced accuracy. The SoC may decrease to zero suddenly. If this happens, [low battery failsafes](emergency-procedures.md#low-battery) (RTL and Land) will be triggered, causing the aircraft to climb or descend suddenly.

These failsafes can be overridden by selecting another flight mode (override by moving the sticks is not available during a failsafe). The battery will not cut off power output in the air, however low temperatures generally reduce capacity which will reduce flight time.

If the batteries are 10 °C or warmer at the start of a flight, heating from discharge will keep them warm enough to fly.

To keep batteries warm, charge them in a heated environment and store them in an insulated container (a cooler works well)

{% hint style="danger" %}
In rare cases, propellers can experience icing. This occurs when ice begins to form on the tips and underside of the blades due to temperature and humidity. This will cause the props to become unbalanced, increasing drag and reducing lift. Flying with iced blades can be dangerous and is not advised.
{% endhint %}
{% endtab %}
{% endtabs %}

{% hint style="warning" %}
Keep the legacy Herelink controller out of direct sunlight. It can operate at up to 50°C ambient _if it's plugged in for charging and in the shade._&#x20;

\
The legacy Herelink controller will shut down if the internal temperature increases over 55C, and it does not give a warning. Direct sunlight can increase the temperature of the Herelink beyond this limit very quickly.&#x20;

\
For the best performance in hot or cold weather, we recommend charging the Herelink during use. Under very hot or cold weather Herelink's battery performance can drop quickly and can cause it to shutdown.
{% endhint %}

### Wind

Operating Astro at winds greater than 8-10m/s can be dangerous. Keep in mind that the wind speed at higher altitudes is typically much higher. In high wind, AMC will show a warning.

Flying Astro in high wind is not advised. If the wind speed is a significant fraction of [Astro's top speed](https://freefly.gitbook.io/astro-public/astro/specs-and-interfaces/performance#flight-speeds), control authority will be diminished in all flight modes.

When Astro is not flying, fold the props and install the propeller protectors. If the wind blows through open props, it can cause them to spin up dangerously.

### Rain and Dust

Astro can operate in moderate rain (approximately 3 mm per hour). [USGS has a guide (scroll to bottom)](https://water.usgs.gov/edu/activity-howmuchrain-metric.html) to help translate between forecasts like "shower" or "drizzle" to accumulation amount.

Battery connectors cannot be mated while wet or containing debris. We recommend compressed air to clean the connectors.

#### Tips for operating in Rainy and Dusty environments.

Rain in particular increases the risk of electrical malfunction because it can lead to short circuits

Dust carries a risk of mechanical malfunction because it can enter the motors and obstruct rotation.

Both of these conditions carry an increased risk of malfunction and danger. It is difficult to judge the exact amount of precipitation, and the amount can vary without warning during the course of a flight. Therefore, we recommend avoiding situations that endanger people.

***

## Voltage Mismatch

If the two batteries powering Astro have a voltage difference of more than 2.0V, a voltage mismatch error will occur. 2V is roughly a 25% difference in the batteries' states of charge.&#x20;

***

## Magnetic Interference

In a situation where there is a magnetic interference, you are presented with a few options:

* Move away from any potential sources of magnetic interference, like metal. In most cases, moving the Astro a few feet away will allow it to get a better magnetic reading to figure out the heading, and position mode will become available for takeoff.&#x20;
* Recalibrating sensors, away from magnetic interference.
* Take off in altitude mode. Shortly after flying in altitude mode, GPS heading will be locked and you can then switch to position mode.

{% hint style="warning" %}
Be aware that flying in Altitude Mode does introduce additional risk. If the aircraft loses connection with the controller, it will not hold its horizontal position which may result in a crash if control is not re-established quickly. &#x20;
{% endhint %}

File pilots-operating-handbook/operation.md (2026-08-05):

---
icon: drone-front
---

# Flight Part 2 - Operation

{% hint style="warning" %}
Make sure you understand Astro's [Emergency Procedures](emergency-procedures.md) and understand how to operate the drone in [Manual Mode](flight-modes.md#manual) before taking flight.&#x20;
{% endhint %}

## Astro Flight Checklist

Below is our recommended Astro flight checklist, which covers the main considerations you need to be aware of before, during, and after operation.&#x20;

{% file src="../.gitbook/assets/Astro Checklists and EPs - v5.pdf" %}
Astro Checklists and EPs - v5.pdf
{% endfile %}

We also offer this checklist as a [Google Sheet template](https://docs.google.com/spreadsheets/d/1fzej5xve3mPZBkT5TpqMw7kgLpMkx0kWQzTIOoPZfCs/edit?usp=sharing) to allow for a more customized experience. For example, you might want to add specific items to better reflect your company's safety procedures, workflow, payload, or region.&#x20;

***

## Before Flight

### Powering On the Transmitter

{% tabs %}
{% tab title="Pilot Pro" %}
If you have a Tab 3 (red button on the tablet) press and hold the small black button on the edge of the tablet to turn it on

If you have a Tab 5 (green button on the tablet) press the power button on the Pilot Pro twice

{% hint style="warning" %}
Pilot Pro will automatically open the Pilot Pro App. Once the Astro is running and everything shows as connected, switch over to the AMC app
{% endhint %}
{% endtab %}

{% tab title="Legacy Herelink" %}
Press and hold the power button below the screen until you see the Herelink logo appear
{% endtab %}
{% endtabs %}

### Powering On the Astro

{% embed url="https://www.loom.com/share/9fd36b44a09f4a0e871f2d61f6438ba0" %}
How to power the Astro
{% endembed %}

The Astro can be powered with either one or two batteries. One battery will put the Astro into Bench Mode to prevent arm for benchtop operations, and two batteries will allow for flight

{% hint style="warning" %}
Bench Mode: Astro will only arm (i.e. spin the motors) if 2 batteries are installed. When powering Astro for non-flying purposes (e.g. bench testing), connect only one battery.

Bench mode is not a substitute for the absolute safety of removing propellers.
{% endhint %}

To power on the Astro, connect at least one SL8 battery by sliding it along the rails on top of the aircraft until you hear two clicks. Once connected, press the button on the battery twice to turn it on. If you have two batteries connected, they will both automatically power on when you turn on one of them.&#x20;

### Checking Battery Levels

{% tabs %}
{% tab title="First Tab" %}
With Pilot Pro, AMC will show the Astro's current battery levels. Tap on the battery icon for more information, such as remaining flight time.&#x20;

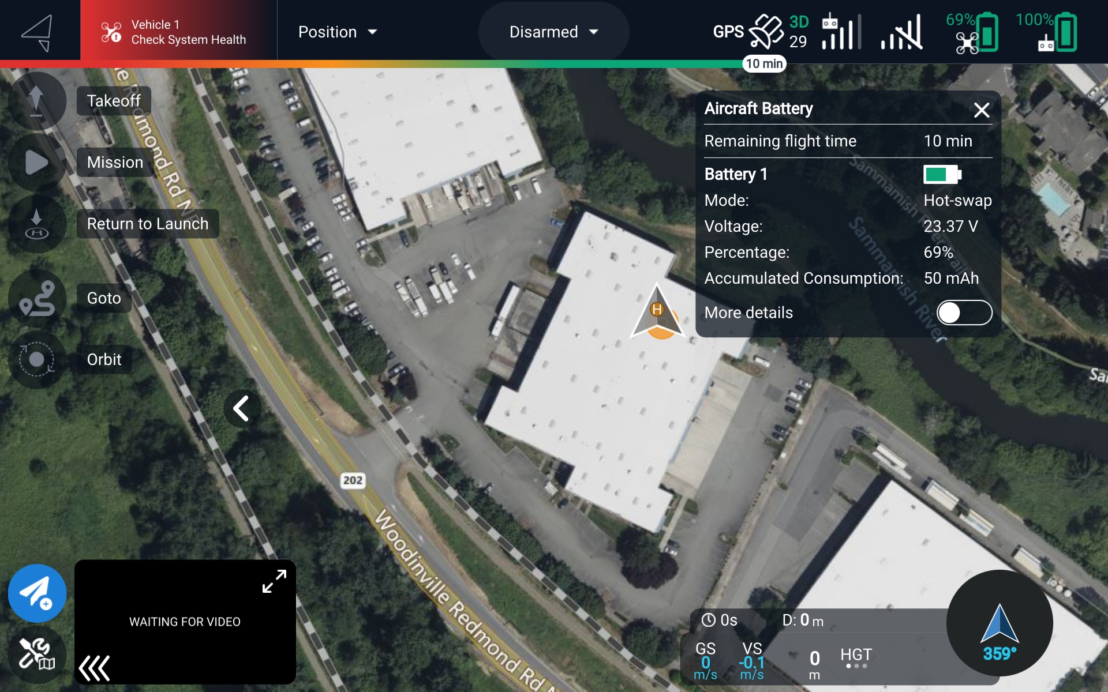
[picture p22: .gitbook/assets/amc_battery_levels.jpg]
<figure><figcaption></figcaption></figure>

{% hint style="info" %}
The battery level for the RC will almost always report 100% at all times, because the Pilot Pro keeps the tablet fully charged. &#x20;
{% endhint %}
{% endtab %}

{% tab title="Legacy Herelink" %}
Once the transmitter and Astro are connected, the AMC app indicates Astro's battery level and the battery level of the handset in the status bar.

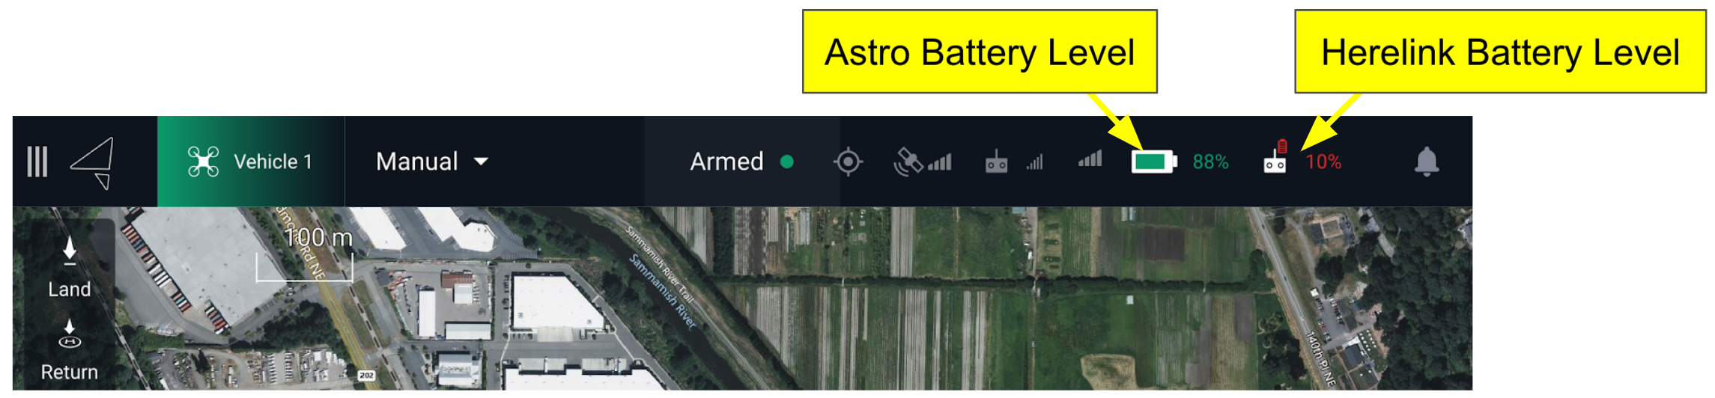
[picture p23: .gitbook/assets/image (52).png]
Where to find Astro and Handset battery levels in AMC

{% endtab %}
{% endtabs %}

### Issues Preventing Arming

You may occasionally encounter issues that will prevent Astro from arming:&#x20;

#### Compass Cal

If AMC asks you to calibrate the compass and won't allow you to take off, follow the [instructions to recalibrate sensors](../maintenance/standard-maintenance-procedures/calibration-and-tuning.md#sensor-calibration) in an area without significant magnetic interference (far from large metal structures or magnetic/electric installations).&#x20;

#### Everything else&#x20;

Check if the AMC message you're encountering is on our [Error/Warning Spreadsheet](https://docs.google.com/spreadsheets/d/1DXkk0BmRx9qLbjpBt2KgKYFOQhEGUTcyyQB6rOmb4ac/edit#gid=0) and follow the associated instructions. If you're still experiencing the issue, please reach out to support@freeflysystems.com for further troubleshooting.&#x20;

***

## Arming and Disarming

Astro's propulsion system has two fundamental states: Disarmed and Armed. These states are displayed on the Astro through the LED's on the boom arms.&#x20;

| State | Definition | Indication |
| --- | --- | --- |
| Disarmed | Safe mode, no spinning propellers | Boom LEDS dim |
| Armed | Aircraft will spin propellers, ready to fly | Boom LEDs bright (100% or user specified level) |

Astro can be armed with or without GPS.&#x20;

{% hint style="info" %}
Pro Tip: Wait for GPS lock even if you don't plan to use Position Mode because Return Mode relies on GPS.
{% endhint %}

{% hint style="danger" %}
Before arming, ensure people and other obstacles are clear of the propellers. Be prepared for Astro to take off.
{% endhint %}

The transition between Armed and Disarmed can be done either [through AMC](https://freefly.gitbook.io/astro-public/pilots-operating-handbook/emergency-procedures#advanced-arming-methods) or with the sticks on the pilot handset. (The pilot's handset default configuration is [Mode 2](https://docs.px4.io/master/en/getting_started/rc_transmitter_receiver.html#types-of-remote-controls).)

| State | Input |
| --- | --- |
| Arming (Mode 2) | Hold the throttle stick down and right for 2 seconds. |
| Disarming | When the aircraft has landed, continue holding the throttle stick down for 2 seconds. |

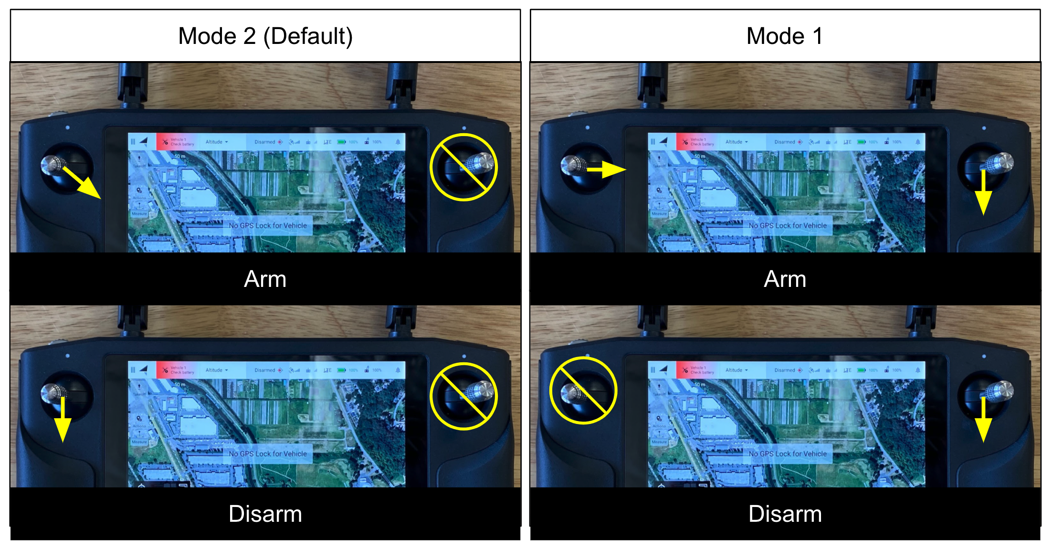
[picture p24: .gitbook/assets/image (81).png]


{% hint style="info" %}
It is not possible to disarm via the normal method while in flight.

To disarm during flight, perform an [Emergency Stop](https://freefly.gitbook.io/astro-public/astro/pilots-operating-handbook/emergency-procedures#emergency-stop).
{% endhint %}

{% hint style="info" %}
If Astro does not arm, check [Auterion Mission Control (AMC) for errors or warnings](essential-software/auterion-mission-control/).
{% endhint %}

{% hint style="info" %}
Use only the throttle stick to Arm & Disarm. Astro will not respond to two-stick input (i.e. DJI arming gesture).
{% endhint %}

Missions may Arm and Disarm the aircraft automatically. For example, if a mission is started while the aircraft is disarmed on the ground, the aircraft will arm and take off.

### Automatic Disarm Methods

Under these conditions, Astro will automatically disarm.

| Method | Astro behavior |
| --- | --- |
| Ground timeout before taking off | If Astro sits on the ground at idle throttle for 10 seconds, it will automatically disarm. |
| Land mode | If Astro is in Land Mode, and detects a landing, it will disarm after 2 seconds. For example, this applies if the last command in a mission is "Land". |

***

## Taking off

Position Mode is best for taking off in most cases, as it offers the most stabilization. However, it is certainly possible to take off in Altitude, Manual, and Mission modes as well.&#x20;

For 5 seconds after takeoff, the maximum pitch and roll angles are reduced to 12 degrees.

After takeoff, promptly climb out of ground effect (i.e. to 3 meters / 12 feet of altitude) to avoid snagging landing gear on the ground.

#### Takeoff best practices:

{% tabs %}
{% tab title="In Position and Altitude Mode" %}
After arming, allow the throttle stick to return to the center. The propellers will remain idle. When ready to take off, raise the throttle stick. The propellers will spin up and the aircraft will take off.
{% endtab %}

{% tab title="In Manual Mode" %}
After arming, hold the throttle stick straight down with no Yaw input. When ready to take off, raise the throttle stick slowly. The propellers will accelerate as soon as the throttle stick moves. As the throttle approaches the mid-point, there will be enough thrust to take off. Continue raising the throttle to achieve a brisk takeoff.
{% endtab %}
{% endtabs %}

***

## Landing

Position Mode is best for landing in most cases, as it offers the most stabilization. However, it is certainly possible to land in Altitude and Manual modes as well. The aircraft behaves a little differently in each mode.

{% hint style="danger" %}
Do not hand catch Astro. The aircraft is designed to be landed on hard flat surfaces. Hand catching can result in serious injury or death.
{% endhint %}

In Position and Altitude Modes, at altitudes below 7 meters, the maximum vertical speed is reduced to 0.7 m/s (from the normal value of 2 m/s).

Astro will disarm automatically after the autopilot detects a landing. Landing detection brings together input from several sensors to determine when it is safe to disarm.

{% hint style="warning" %}
If the landing is not detected (i.e. the props do not stop after touchdown), perform the [Emergency Procedure for Landing Detector Failure](emergency-procedures.md#emergency-stop-amc).
{% endhint %}

#### Landing best practices:

{% tabs %}
{% tab title="Landing In Position Mode" %}
Bring the aircraft to a hover > 2 meters over the spot where landing is desired. Pull the throttle stick straight down as far as it goes, without any pitch, roll, or yaw commands. Astro's landing sensor will manage the speed of your descent. After touchdown, hold the throttle stick down until Astro disarms and the propellers stop.

At altitudes below 2 meters, the maximum pitch/roll angle is reduced to 12 degrees. This prevents abrupt maneuvers that might cause a tip-over.

{% hint style="warning" %}
Pitch, Roll, or Yaw commands very near the ground can cause crashes or tip-overs.
{% endhint %}
{% endtab %}

{% tab title="Landing In Altitude Mode" %}
Landing in Altitude Mode is different than Position Mode because the pilot is responsible for managing lateral velocity. The autopilot will control the throttle to manage the descent rate.

Bring the aircraft to a hover > 2 meters over the spot where landing is desired. Give minimal pitch and roll commands to minimize both lateral speed and minimize pitch/roll angle. Pull the throttle stick down. After touchdown, hold the throttle stick down until Astro disarms and the propellers stop.

At altitudes below 2 meters, pitch/roll angle limits are reduced to 12 degrees. This reduces the likelihood of abrupt maneuvers that might cause a tip-over.
{% endtab %}

{% tab title="Landing In Manual Mode" %}
Landing in Manual Mode is different than Position or Altitude Mode because the pilot is responsible for managing vertical _and_ lateral velocity.

Bring the aircraft to a hover > 2 meters over the spot where landing is desired. Give minimal pitch and roll commands necessary to minimize both lateral speed and minimize pitch/roll angle. Reduce throttle to allow the aircraft to descend slowly.

As Astro nears the ground and enters ground effect, the pilot will often need to reduce the throttle to keep the aircraft descending. Once the aircraft has touched down, the operator should reduce the throttle to zero promptly so that it settles on the ground instead of possibly bouncing or dragging the landing gear. Hold the throttle stick down until Astro disarms and the propellers stop
{% endtab %}
{% endtabs %}

***

## Battery Changes / Hotswaps

{% hint style="danger" %}
While Astro will recognize that the battery is low and perform a failsafe action (return to launch by default), the aircraft has no context of situations that might prevent a safe landing before the battery is exhausted. For instance, if the aircraft is several miles away from the RTL point when the failsafe is triggered, there is a chance that there won't be enough battery life to return. \
\
It is the pilot's responsibility to determine the appropriate time for a battery change and to ensure the aircraft is safely grounded.
{% endhint %}

### Battery Changes

The Astro's batteries can be removed by pushing up on the grey tab on the back of the battery. This will unlock the battery, and allow you to slide it out.&#x20;

{% hint style="info" %}
Astro's SL8 batteries do not need to be powered off before removal
{% endhint %}

### Hotswap

{% embed url="https://www.loom.com/share/777a0228e2534723910acf0e2d48456a" %}

During some longer missions, you may find hotswapping batteries easier, which will keep the Astro powered on during the battery changing process. To hotswap batteries, remove one discharged pack from the drone and replace it with a charged pack. Enable the pack by pressing the power button twice, then replace the other discharged pack. Enable the second charged pack if it does not show "Hotswap" on the battery display screen.&#x20;

The pilot may also adjust the [Low Battery Failsafe settings](https://docs.auterion.com/vehicle-operation/settings-and-maintenance/safety#low-battery) to activate Return Mode automatically at a level appropriate for the mission.&#x20;

Upon landing, AMC will offer an option to "Resume Mission from Waypoint #". This will modify the mission by removing the waypoints already visited.

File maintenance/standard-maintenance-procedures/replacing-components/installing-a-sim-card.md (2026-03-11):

# Installing a SIM Card

### Installing a SIM in Astro

1. Select nano SIM card and carrier of your choice which falls in the RF Bands Astro supports.
   1. AT\&T and Verizon are recommended. T-Mobile has also been tested and proven functional.
   2. [LTE Band Information Link](https://freefly.gitbook.io/freefly-public/products/astro/pilots-operating-handbook/systems#lte)
2. Ensure Astro is powered down and flip it over so it is resting on its prop-protectors
3. Using a 1.5mm hex driver open the SIM access port and remove the rubber cover.
4. Insert your SIM card and ensure that it has latched into the SIM slot.
5. Reinstall the SIM card cover making sure that the cover seals out the SIM port fully. Then flip Astro back over so it is standing on its landing gear.

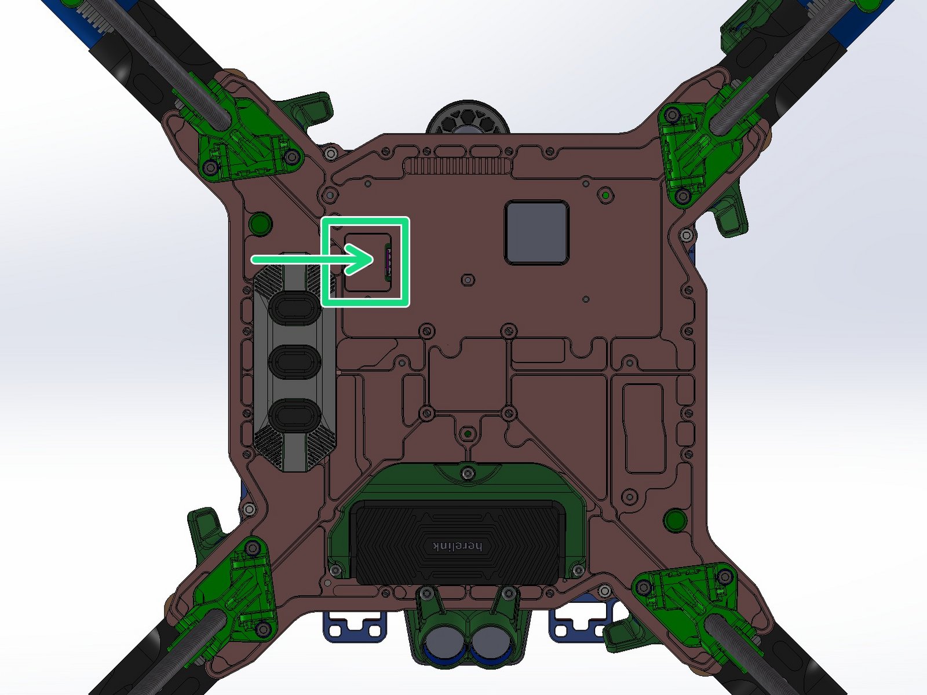
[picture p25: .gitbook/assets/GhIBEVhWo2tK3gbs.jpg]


{% hint style="info" %}
Note: Only North American SIM cards are currently supported by Astro.
{% endhint %}

### Setting up your SIM card&#x20;

1. Browse to [http://suite.auterion.com](http://suite.auterion.com) and navigate to the 'Vehicles' page.
2. Under 'Vehicles' find the vehicle that matches the Astro's serial number.
3. Select your Vehicle, proceed to the Data tab, and then click “Associate SIM Card” .
4. Type in the SIM card number and select 'Associate'. Wait until the Suite refreshes and the SIM is associated with Astro
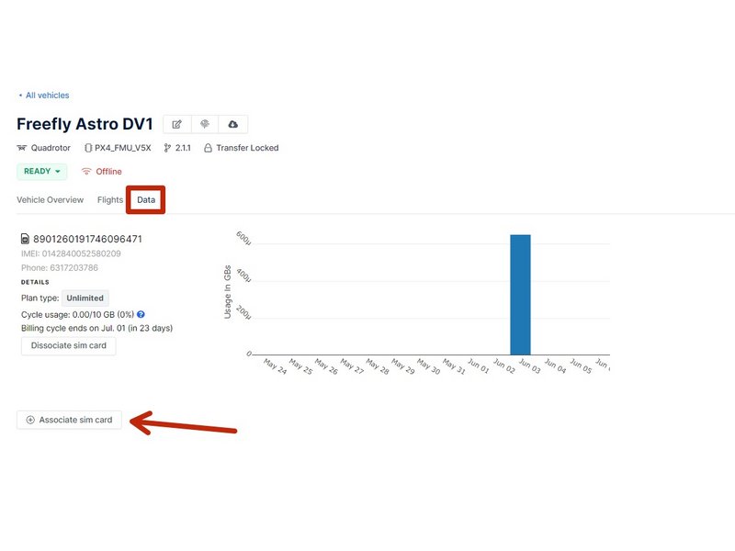
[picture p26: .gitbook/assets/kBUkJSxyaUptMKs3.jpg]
   1. You may get a warning that data is not yet available, this may happen if the SIM has just been activated or no data has been transmitted to the Suite via LTE.
5. Turn on Astro and the Herelink controller.
6. Navigate to the Cellular setup menu under 'Vehicle Setup' on AMC.
7. Ensure that the screen resembles the one shown in the image.
   1. If everything is greyed out, make sure the Astro has had time to fully connect to the Herelink and then try restarting the AMC app on the Herelink controller.
8. Check the box to enable a cellular connection and then enter in your SIM card's APN address.
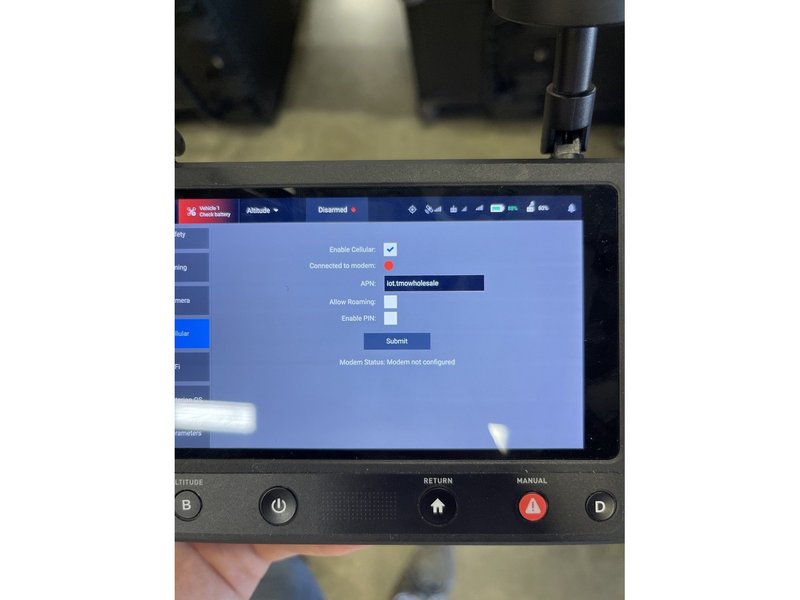
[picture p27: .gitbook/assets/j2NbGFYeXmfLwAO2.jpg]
   1. You can find the APN by inserting the SIM into your cellphone and checking the APN address under the Cellular or Carrier Network Settings. If the APN is not listed in your phone settings you may need to contact the service provider for the address.
9. Once both fields are completed hit 'Submit' and wait for the 'Connection to Modem' indicator to turn GREEN.&#x20;
   1. If there is an error in the APN or the SIM cannot reach service the modem connection may still indicate RED.

{% hint style="info" %}
You only need to setup the SIM card once! The Cellular menu on AMC will reset on each power cycles and show a RED indicator but the settings will have been saved to the aircraft and data will flow when Astro is located in an area where there is cell service..
{% endhint %}

### SIM Card Options

{% hint style="info" %}
Customers have reported that these SIM cards have worked with Astro on the specified cell phone network. If you do not see your preferred provider, please contact them with your Astro's IMEI number (found on the [vehicle identity](https://docs.freeflysystems.com/astro/pilots-operating-handbook/essential-software/network-and-connectivity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)).

&#x20;Please keep in mind that these claims have not been verified or tested by Freefly. For more information, see the [**LTE** ](https://freefly.gitbook.io/astro-public/astro/pilots-operating-handbook/network-and-connectivity#lte)section of our Network and Connectivity page.&#x20;
{% endhint %}

| SIM Card | Location |
| --- | --- |
| T-Mobile | United States |
| TELUS | Canada |

{% hint style="info" %}
Astro is compatible with the following LTE bands: B2, B4, B5, B12, B13, B14, B25, B26, B66, B71
{% endhint %}

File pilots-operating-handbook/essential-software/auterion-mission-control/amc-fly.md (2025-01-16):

---
description: >-
  The fly screen shows a live feed of either the camera feed or an overhead map
  view.
---

# AMC - Fly

## Camera View

This screen includes a live camera feed, telemetry, and camera/gimbal control. You can also launch uploaded missions or take off using the touch screen.&#x20;

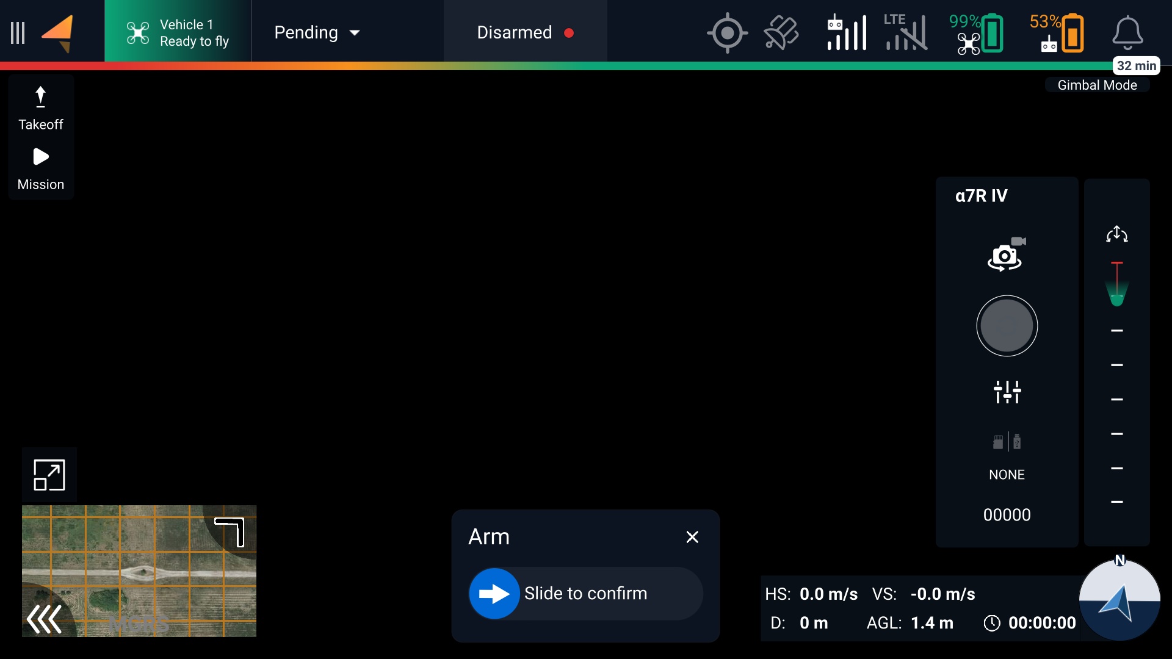
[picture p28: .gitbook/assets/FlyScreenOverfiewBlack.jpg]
<figure><figcaption></figcaption></figure>

## Map View

This screen shows the nearby satellite map, as well as the currently uploaded mission when applicable.&#x20;

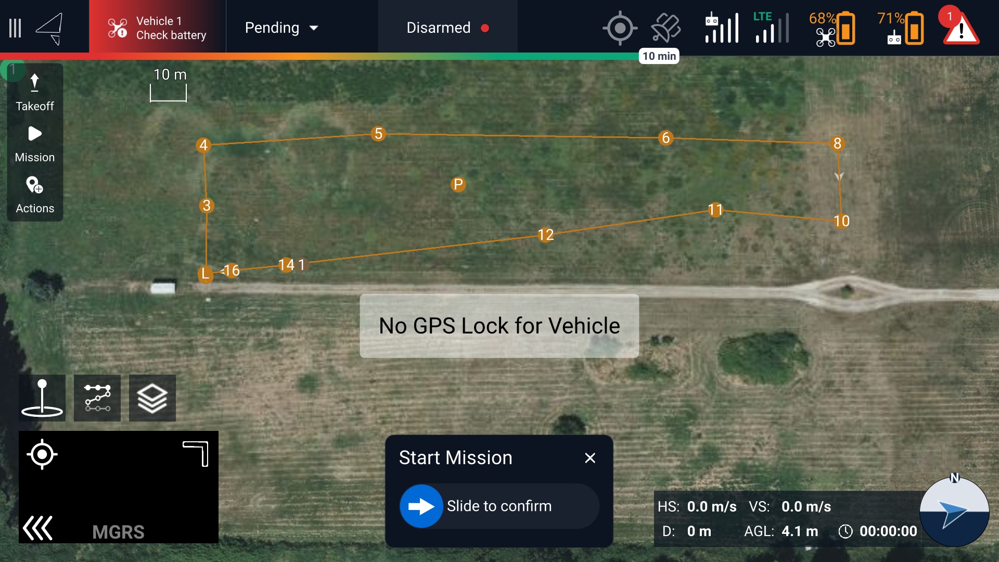
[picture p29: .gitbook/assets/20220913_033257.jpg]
<figure><figcaption></figcaption></figure>

## Pre-Flight Checklist

An optional checklist to assess the requirements of flying a safe mission or manual flight. This checklist can be accessed by tapping the Vehicle box near the top-left corner of the screen. Tapping the yellow boxes turns them green, allowing you to manually verify each item before takeoff.&#x20;

Red items represent warnings or errors. Some items will prevent takeoff if there is an associated warning or error, such as insufficient battery power. Others will allow for takeoff with some limited usage. In the example below, there is no GPS signal, so the aircraft will only be capable of taking off in Manual mode.&#x20;

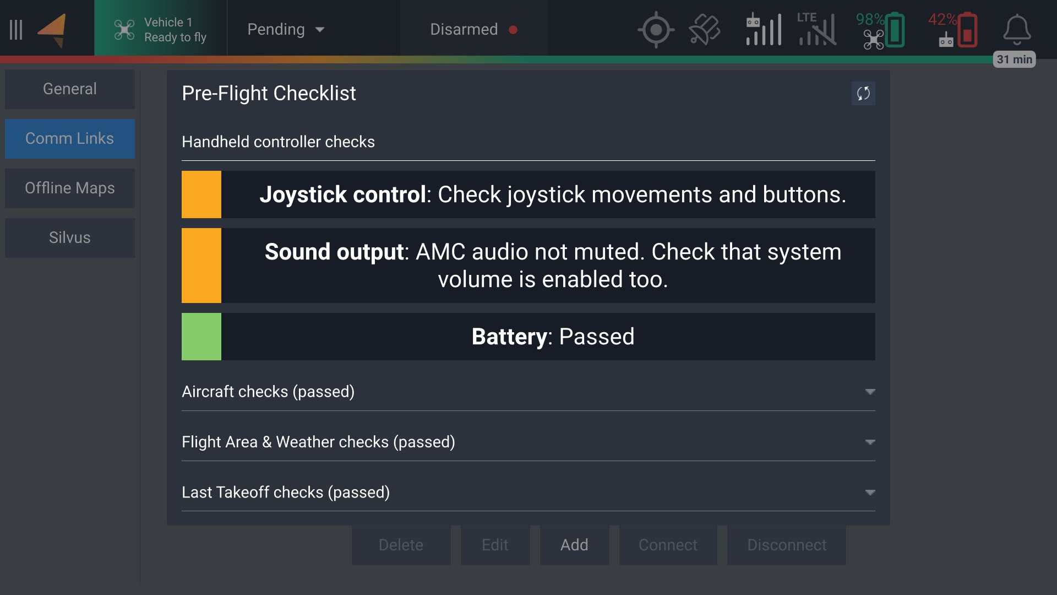
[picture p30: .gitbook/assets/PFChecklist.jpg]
<figure><figcaption></figcaption></figure>

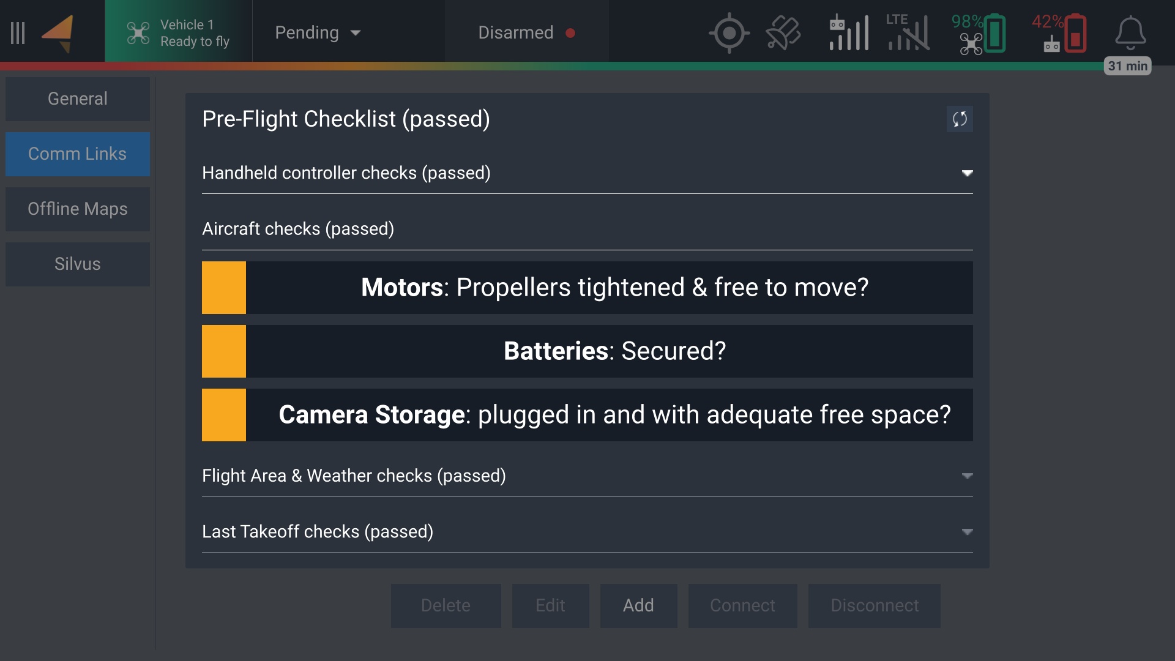
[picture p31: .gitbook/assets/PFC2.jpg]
<figure><figcaption></figcaption></figure>

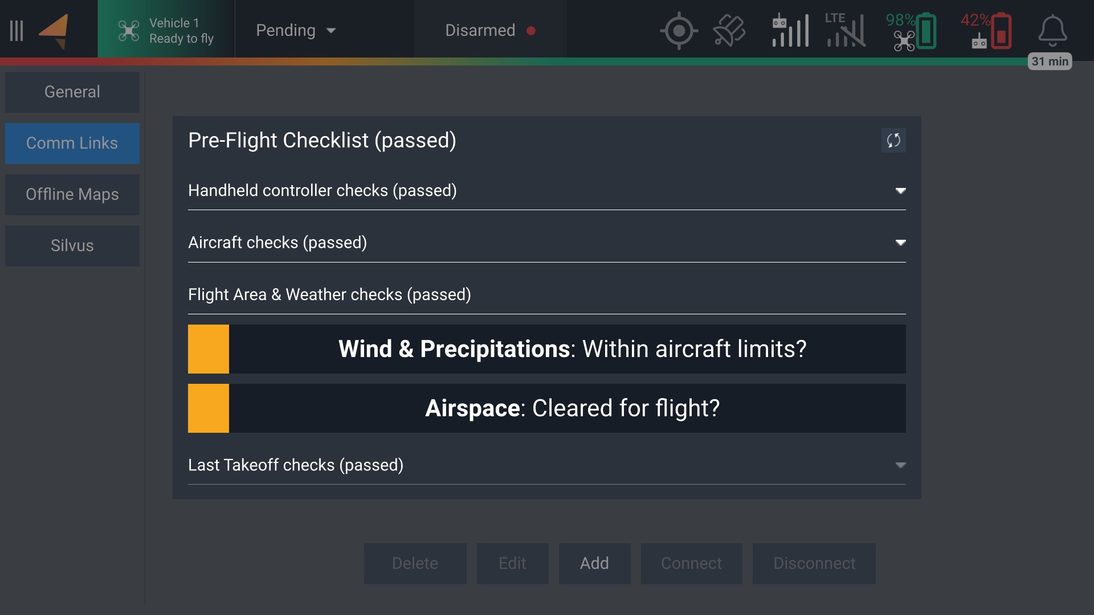
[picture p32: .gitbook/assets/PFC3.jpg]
<figure><figcaption></figcaption></figure>

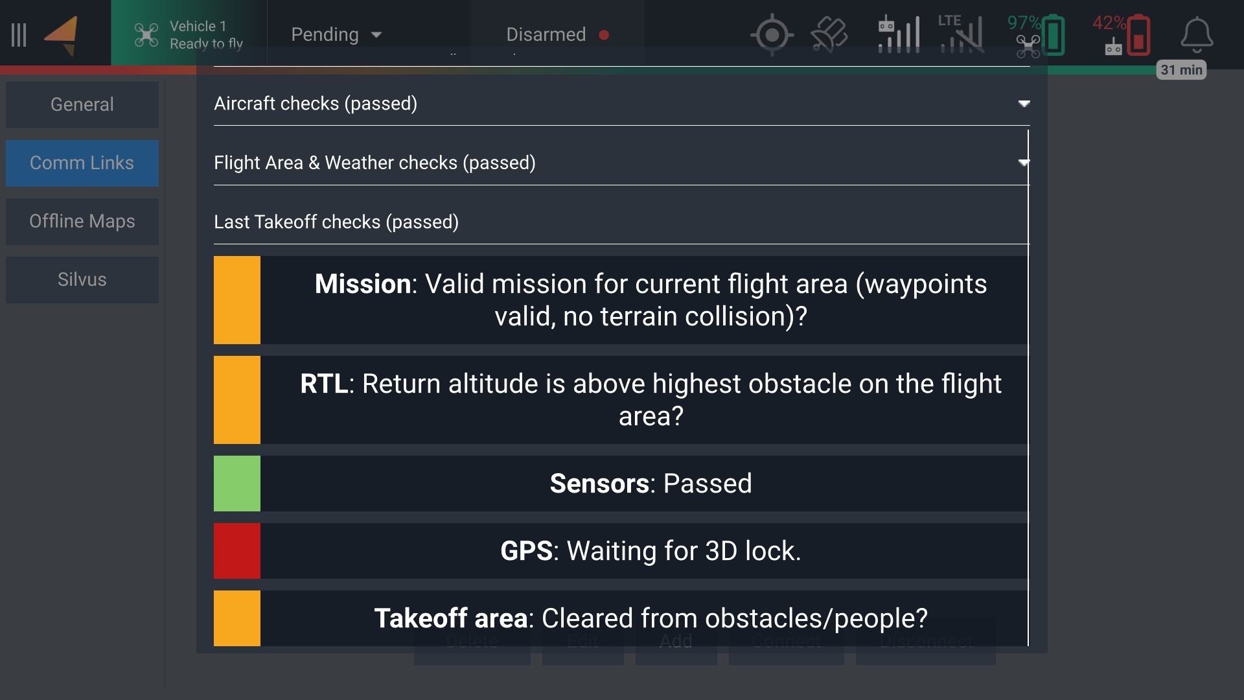
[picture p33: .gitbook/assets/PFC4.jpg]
<figure><figcaption></figcaption></figure>

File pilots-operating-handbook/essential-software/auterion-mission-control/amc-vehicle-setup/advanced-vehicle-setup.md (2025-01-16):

# Advanced Vehicle Setup

Changing these settings requires Advanced Mode, which is not recommended for most pilots. Key safety features and parameters that keep Astro airborne can be disabled if changes are made without understanding their purpose. Keep in mind that changing settings in this mode poses an increased risk to property and safety if not done with careful consideration and care.&#x20;

## Activating Advanced Mode

To switch to Advanced Mode and see many of these options, repeatedly tap on the AMC icon in the top-left-hand corner of the app. After tapping about 6 times, a popup menu will appear asking if you would like to switch to Advanced Mode. The icon will change once Advanced Mode is active. \
\
You can return to Standard Mode by repeating the process of tapping the icon until the menu appears and selecting the option to switch to Standard Mode.&#x20;

## Advanced Summary

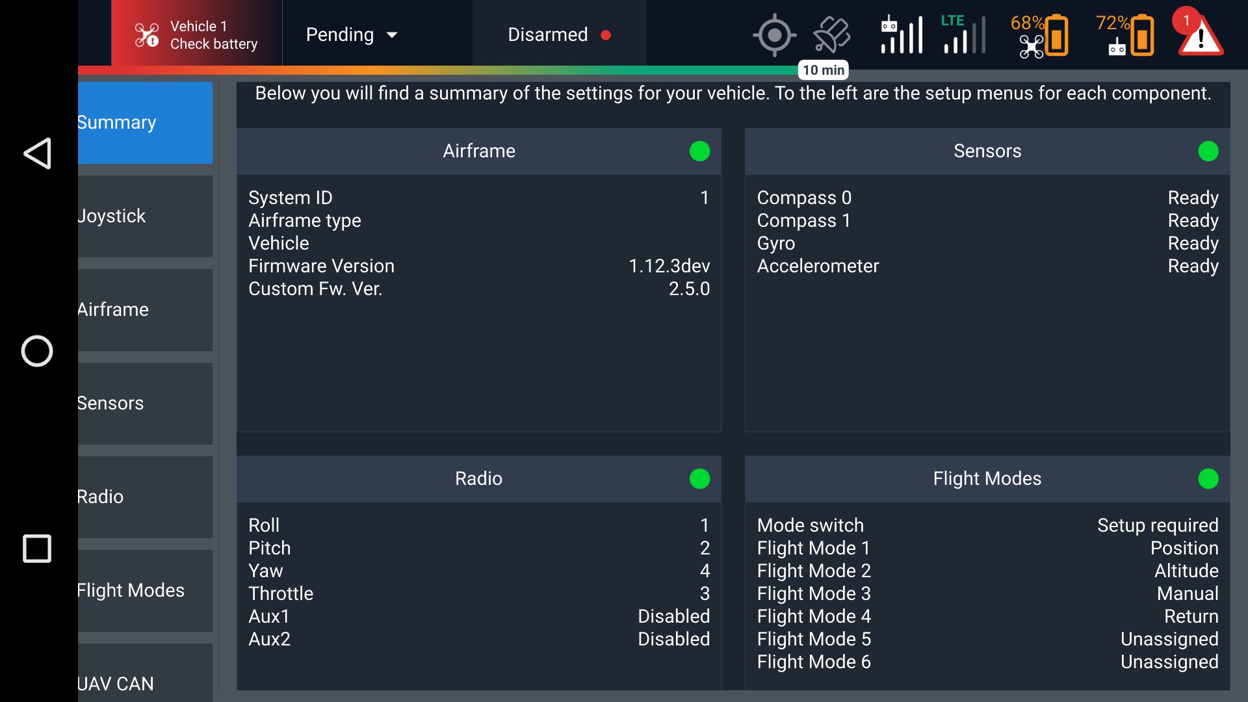
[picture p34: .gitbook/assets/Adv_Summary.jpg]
<figure><figcaption></figcaption></figure>

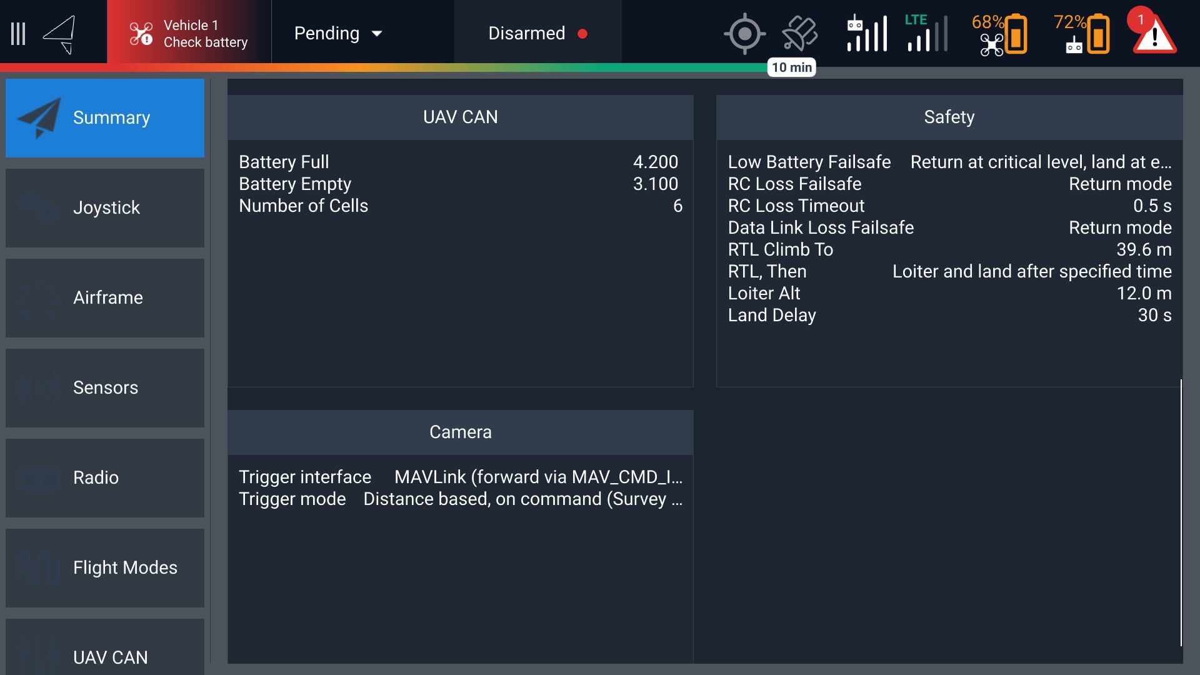
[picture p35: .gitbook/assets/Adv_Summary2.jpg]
<figure><figcaption></figcaption></figure>

## Advanced Airframe

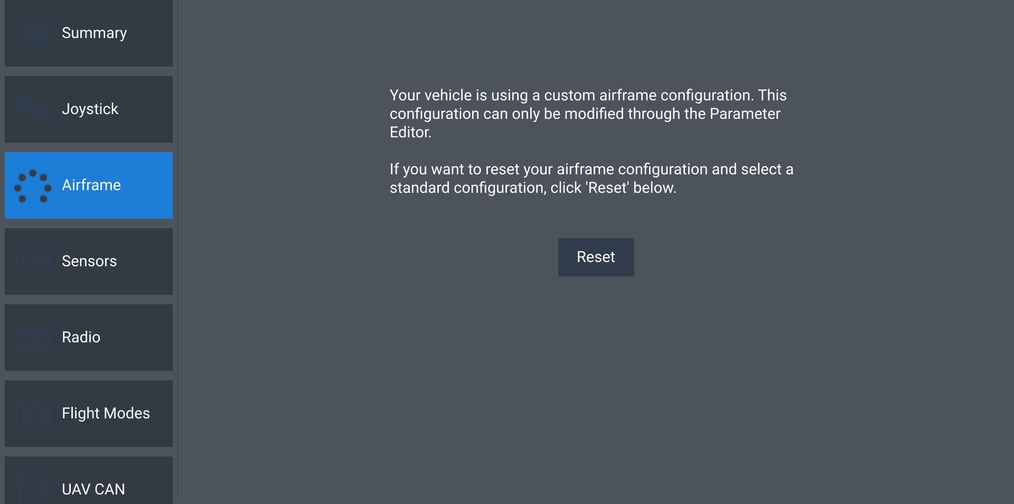
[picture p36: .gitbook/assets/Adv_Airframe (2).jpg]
<figure><figcaption></figcaption></figure>

## Advanced Sensors

Be very careful about the Autopilot Orientation setting when calibrating sensors in Advanced Mode. It should not be changed from the default value of ROTATION\_YAW\_270.&#x20;

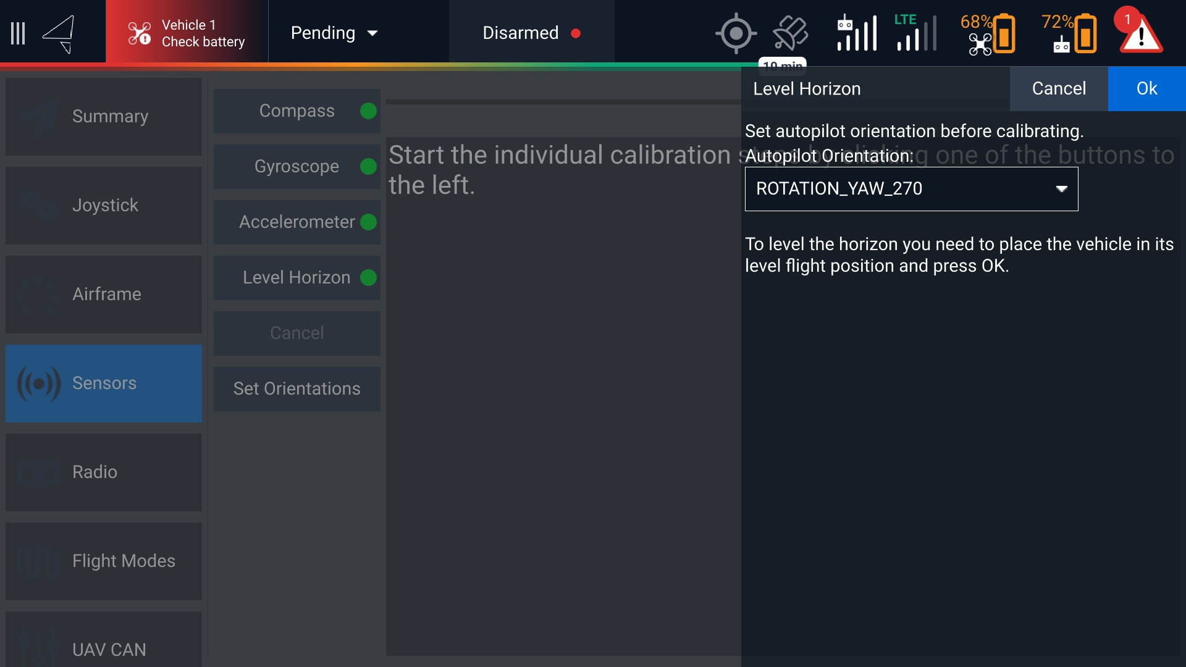
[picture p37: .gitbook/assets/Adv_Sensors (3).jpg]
<figure><figcaption></figcaption></figure>

## Advanced Motors

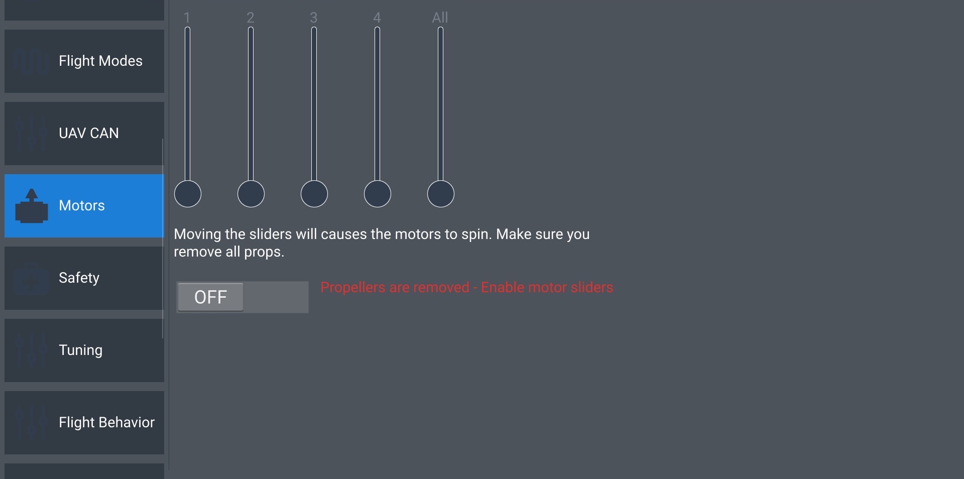
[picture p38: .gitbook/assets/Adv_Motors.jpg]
<figure><figcaption></figcaption></figure>

## Advanced Safety

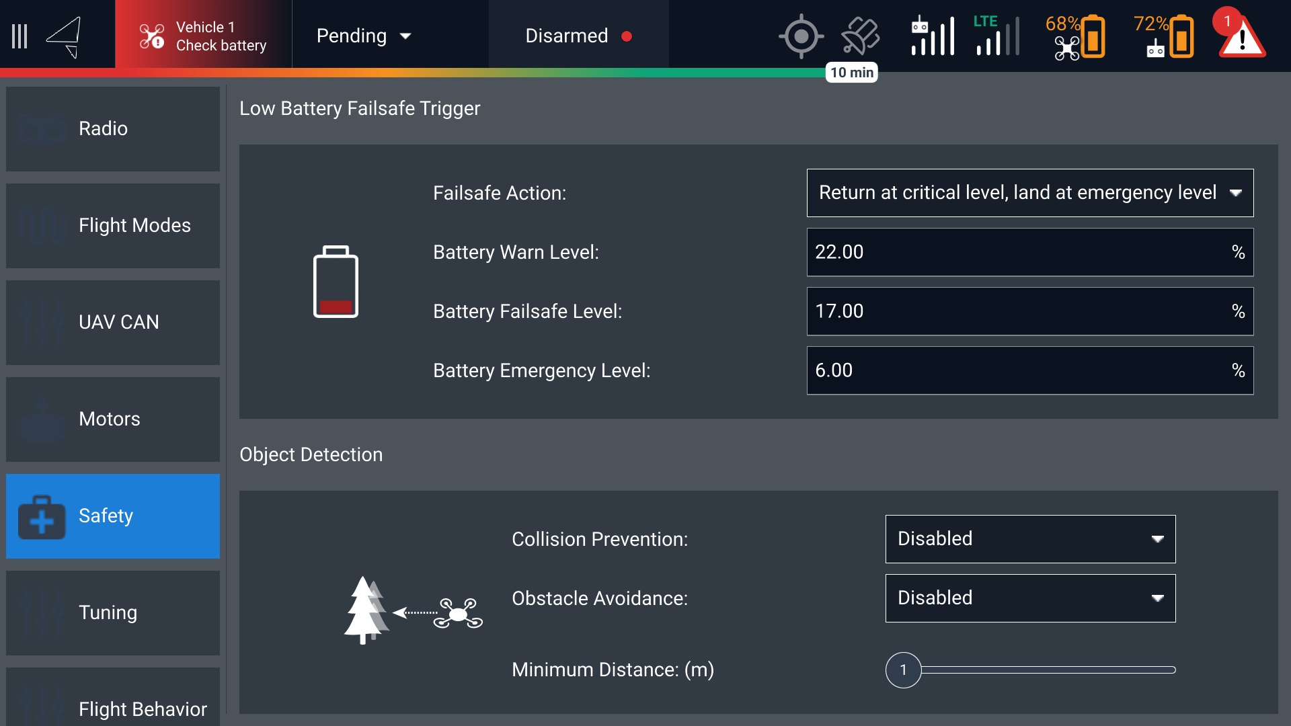
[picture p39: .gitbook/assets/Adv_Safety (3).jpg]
<figure><figcaption></figcaption></figure>

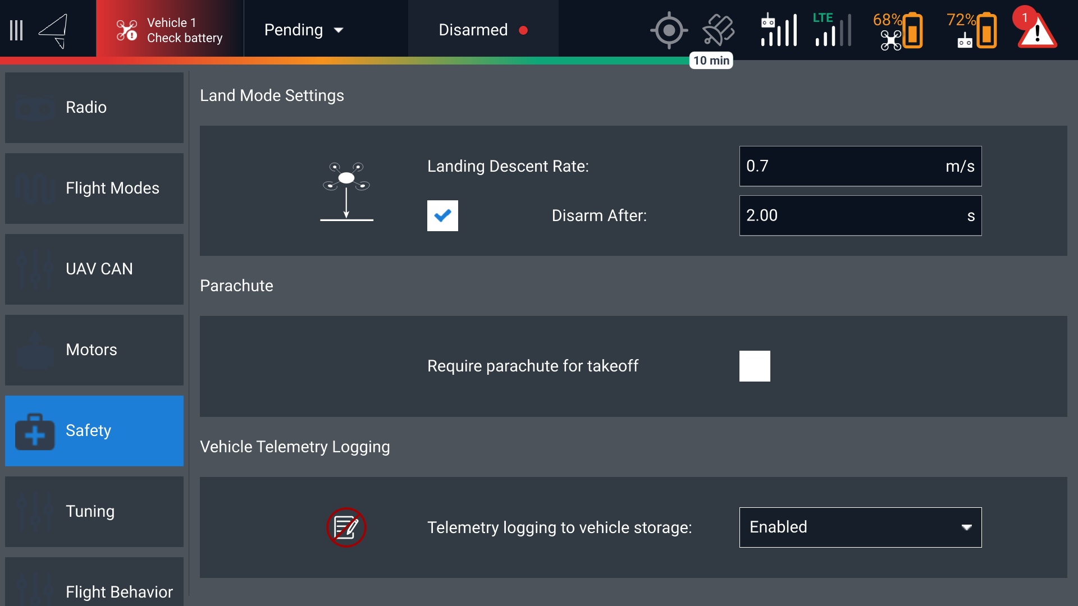
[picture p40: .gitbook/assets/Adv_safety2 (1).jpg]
<figure><figcaption></figcaption></figure>

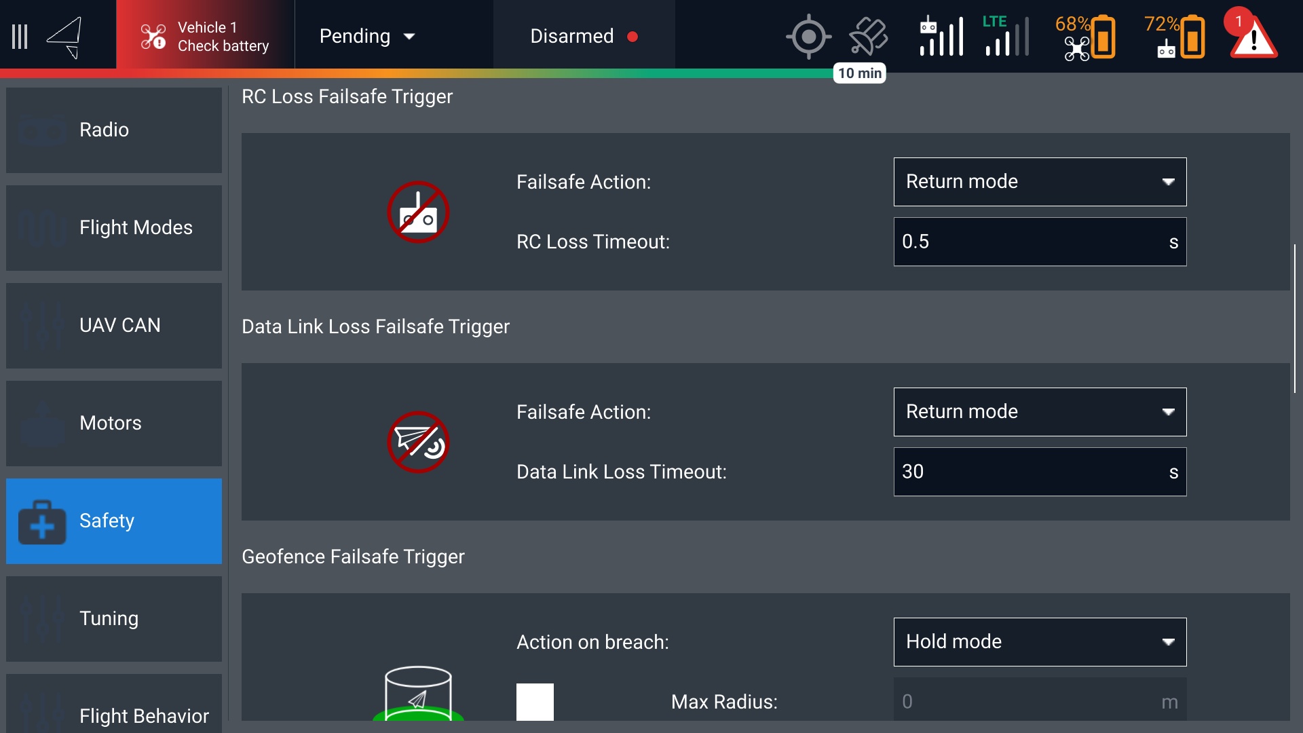
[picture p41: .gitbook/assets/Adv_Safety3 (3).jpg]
<figure><figcaption></figcaption></figure>

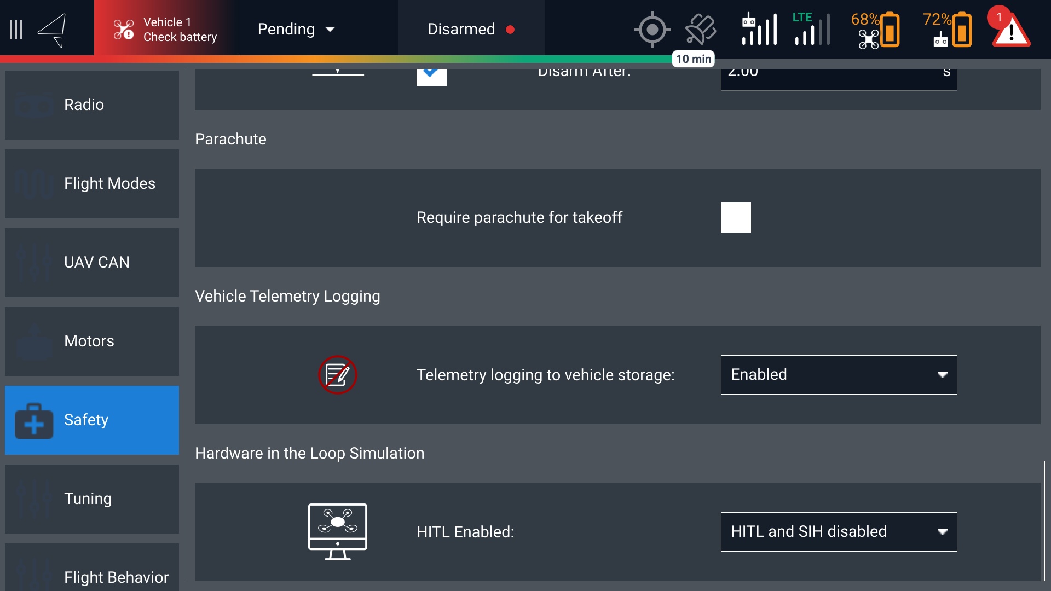
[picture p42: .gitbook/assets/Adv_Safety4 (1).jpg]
<figure><figcaption></figcaption></figure>

## Advanced Tuning

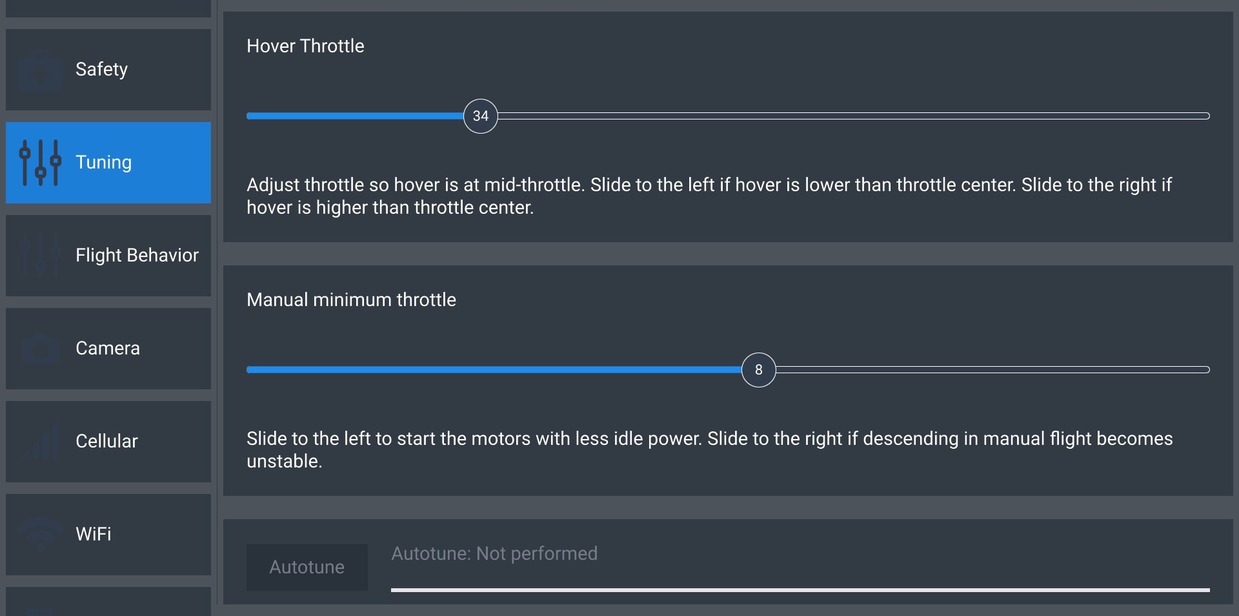
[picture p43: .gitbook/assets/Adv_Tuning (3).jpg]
<figure><figcaption></figcaption></figure>

## Advanced Camera

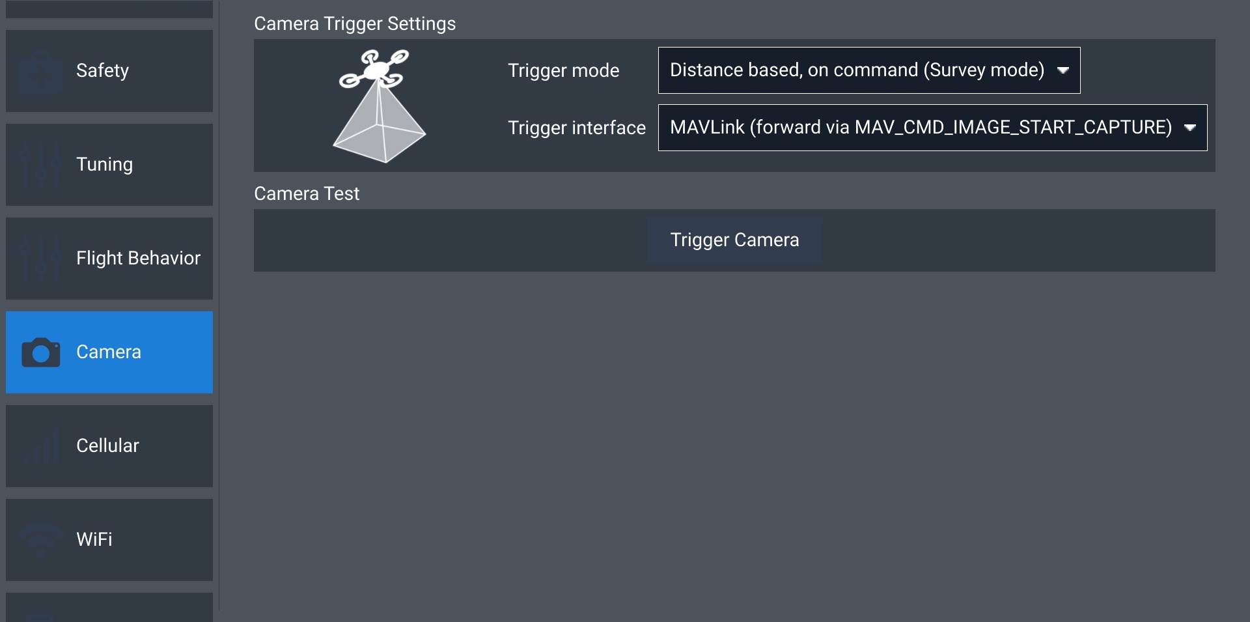
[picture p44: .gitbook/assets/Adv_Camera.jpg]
<figure><figcaption></figcaption></figure>

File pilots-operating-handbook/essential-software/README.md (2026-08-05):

---
description: >-
  Freefly has partnered with Auterion to provide customers an easy way to fly
  using Auterion Mission Control, as well as manage their fleet using Auterion
  Suite.
icon: code
---

# Auterion Software

### [Auterion Mission Control](https://docs.freeflysystems.com/astro/~/revisions/mTpQspqCOZxVfR8CbzgE/pilots-operating-handbook/essential-software/auterion-mission-control)

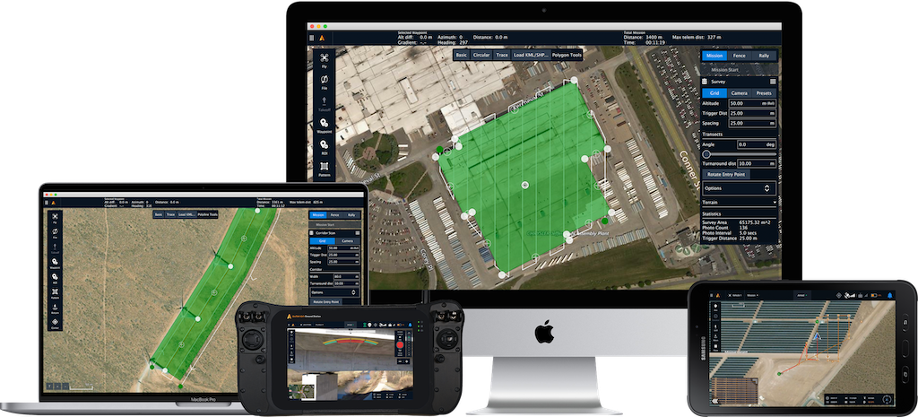
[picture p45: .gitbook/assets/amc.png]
<figure><figcaption></figcaption></figure>

**Auterion Mission Control (AMC)** is the mission planning software pre-installed on Pilot Pro.&#x20;

### [Auterion Suite](https://docs.freeflysystems.com/astro/~/revisions/mTpQspqCOZxVfR8CbzgE/pilots-operating-handbook/essential-software/auterion-suite)

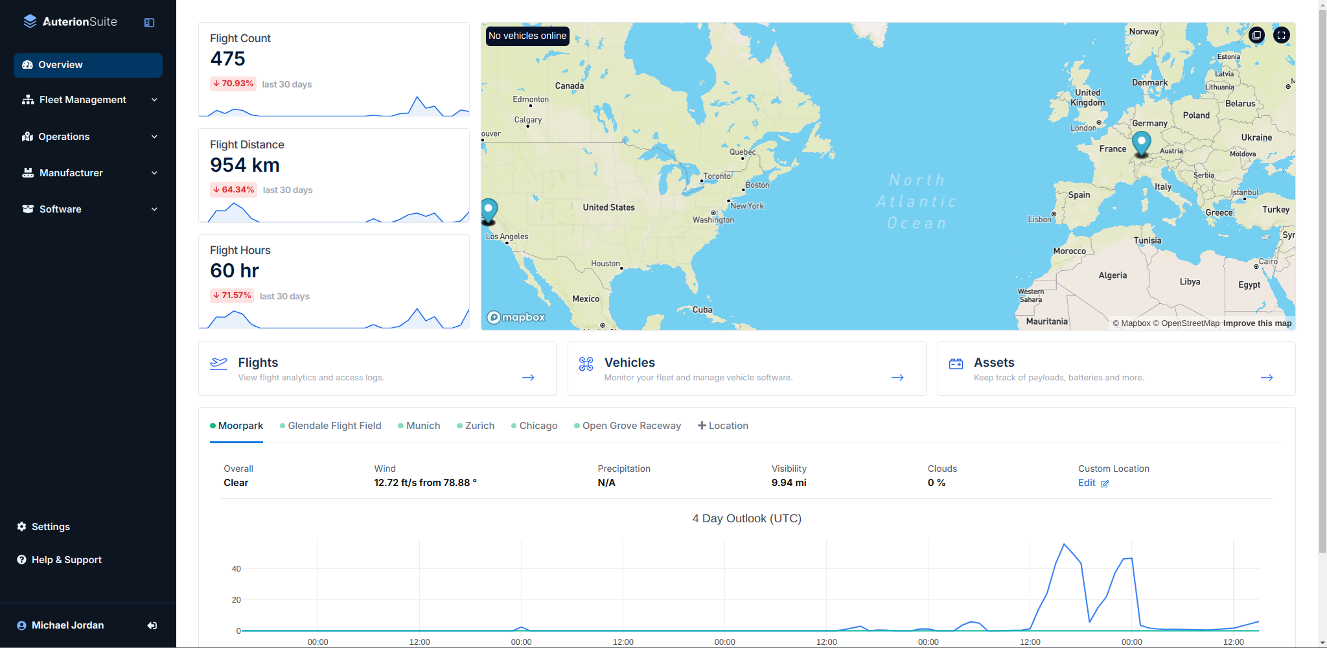
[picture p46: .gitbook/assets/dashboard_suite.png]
<figure><figcaption></figcaption></figure>

**Auterion Suite** is an _optional_ fleet management web app that is fully compatible with Astro. It has useful features like automatic flight log uploads, image uploads, and more. Learn more by visiting [Auterion's documentation](https://docs.auterion.com/vehicle-operation/auterion-suite-fleet-management).

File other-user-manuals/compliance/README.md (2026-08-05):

---
icon: gavel
---

# Compliance

## Remote ID

Freefly provided a no-cost software update for all Astro operators to enable FAA Remote ID compliance in North America with firmware v1.5 or later. Refer to the next section for more information: [faa-remote-identification-rid.md](faa-remote-identification-rid.md "mention")

All new Astro ship with FAA Standard Remote ID enabled.

## Component Sourcing

Astro variants using Herelink radios are not NDAA-compliant, as the Herelink controller and air unit are manufactured in China. \
\
The [Pilot Pro controller with Herelink RF ](https://store.freeflysystems.com/products/pilot-pro)is not NDAA-compliant, as the Herelink air unit is still used on the aircraft. \
\
Astro + Pilot Pro using Doodle Labs radios is NDAA-compliant and DIU Blue Listed.

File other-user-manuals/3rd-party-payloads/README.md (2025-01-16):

# 3RD PARTY PAYLOADS

Astro is designed to be compatible with a wide variety of payloads.

* Astro utilizes the Smart Dovetail which is the reference design for the [Pixhawk Payload Bus Standard](https://github.com/pixhawk/Pixhawk-Standards/blob/master/DS-014%20Pixhawk%20Payload%20Bus%20Standard.pdf)

Want to see your payload listed here? [Click here to tell us about it!](mailto:support@freeflysystems.com)

Want to learn about developing payloads for Astro? Check out the [Interfaces section](../specs-and-interfaces/) of this wiki!

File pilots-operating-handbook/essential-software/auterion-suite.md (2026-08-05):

---
description: A fleet management web app that works with Astro out of the box
---

# Auterion Suite

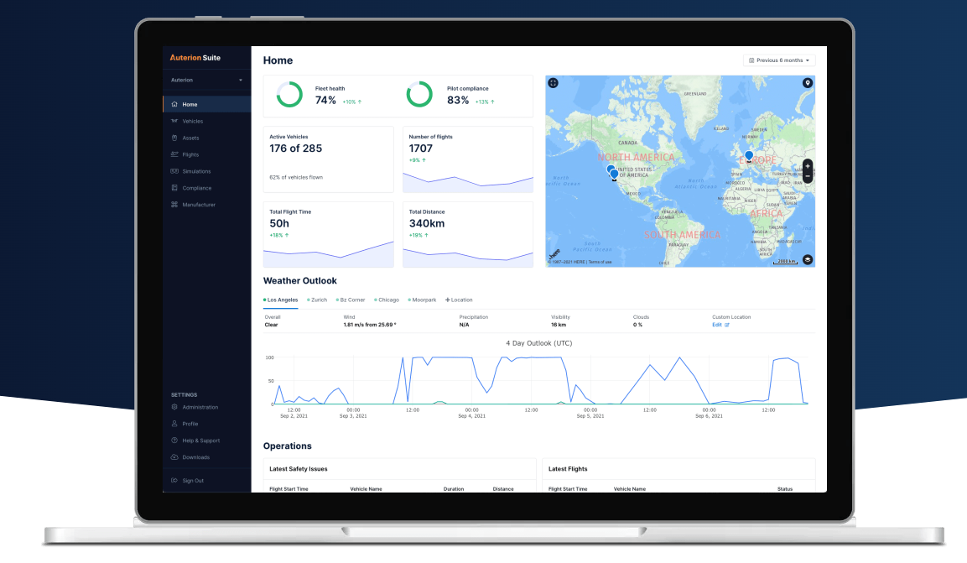
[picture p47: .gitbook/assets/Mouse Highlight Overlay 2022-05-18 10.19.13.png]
Auterion Suite Dashboard


### Overview

Auterion Suite is an optional, paid fleet management web app that is fully compatible with Astro. It has useful features like automatic flight log uploads, image uploads, and more. Learn more by visiting [Auterion's documentation](https://docs.auterion.com/vehicle-operation/auterion-suite-fleet-management).

Many features are available, such as:

* Managing your aircraft fleet
* Access detailed flight logs, and easily share them with Freefly Support
* Get software updates
* Cloud features like log upload, image upload, live streaming, and more.

{% hint style="info" %}
To start using Auterion Suite, you must [sign up for an account](https://docs.auterion.com/vehicle-operation/auterion-sign-up).
{% endhint %}

{% hint style="info" %}
Auterion Suite is _optional_. It will not prevent you from flying your aircraft.&#x20;

There is a free version with limited functionality. A paid subscription is required to unlock all its features. For more information on pricing and features, see below.
{% endhint %}

### Basic (Free) Plan vs. Pro Plan&#x20;

<table data-search="false"><thead><tr><th width="230.71429443359375"></th><th width="178.4935302734375">Basic (Free)</th><th width="263.15582275390625">Pro</th></tr></thead><tbody><tr><td>Price</td><td>$0</td><td><p><strong>$77</strong> per vehicle/month, billed annually</p><p>OR<br><strong>$95</strong> per vehicle/month, billed monthly</p></td></tr><tr><td>Vehicles</td><td>Up to 2</td><td>Up to 15</td></tr><tr><td>Collaboration</td><td>Up to 5 users</td><td>Up to 40 users</td></tr><tr><td>Battery Monitoring</td><td>Up to 4 batteries</td><td>Up to 100 batteries</td></tr><tr><td>Missions</td><td>Up to 5 missions</td><td>Up to 100 missions</td></tr><tr><td>Pilot Certification Management</td><td>None</td><td>Yes</td></tr><tr><td>Reporting</td><td>Yes</td><td>Yes</td></tr><tr><td>Flight Logs</td><td>Up to 7 days</td><td>Unlimited</td></tr><tr><td>Log Download</td><td>No</td><td>Yes</td></tr><tr><td>Live Streaming</td><td>No</td><td>Yes</td></tr></tbody></table>

{% hint style="info" %}
&#x20;After two vehicles, Auterion Suite's Basic plan will not allow additional vehicles to be registered. You will need to either [archive an existing vehicle](https://docs.auterion.com/vehicle-operation/auterion-suite-fleet-management/fleet-management/vehicles#archive), or purchase a Pro plan subscription.
{% endhint %}

For more plan details and updated pricing information, [contact Auterion](https://auterion.com/company/contact-us/).

### How to sign up for the Auterion Suite and Register your Astro

{% embed url="https://www.youtube.com/watch?v=3cfPFp3I17s" %}

**This video covers the workflow to register your Astro with Auterion Suite.**&#x20;

* Using a computer, connect a USB-C cable from your computer to the IO panel on the underside of the Freefly Astro.&#x20;
  * Power on the the Astro with one SL8 battery (NOTE: Using only one battery prevents the danger of accidentally arming the aircraft).&#x20;
  * **This physical connection to the Astro is required for security reasons as the Suite enables location data, live streaming, etc.**&#x20;
* Using a web browser, go to the following address to connect to the Astro: `10.41.1.1`
* This page will allow the user to sign up for the suite as well as automatically register and claim the aircraft. Click "Register Now" or scan QR code for mobile signup.
  * Note: This requires the vehicle to be online to generate a signup QR code otherwise it’ll say “internet required” for the registration prompt.
  * [Connect the Astro to the internet](../../maintenance/network-and-connectivity.md) using either a WiFi or LTE network.&#x20;
  * <div data-gb-custom-block data-tag="hint" data-style="warning" class="hint hint-warning"><p>By default, Blue/NDAA Astros have WiFi and LTE disabled for DIU Blue compliance. </p><p>For more information, see <a data-mention href="../../other-user-manuals/compliance/diu-blue-suas.md">diu-blue-suas.md</a></p></div>
  * If Astro is connected to the internet and plugged into the computer and `10.41.1.1` does not show the Register Now button, try refreshing your browser. &#x20;
* Once complete, you should see the Astro unit listed under the "Vehicles" Section on the main dashboard of the Auterion Suite.
* Go Fly!&#x20;

### Flight Logs

Astro's autopilot automatically creates log files that record the aircraft's flight path, inputs received, outputs sent, and more.

Log files are stored to aircraft's internal storage, which can be downloaded to a PC. If the Astro is configured to upload logs to Auterion Suite, you can view them any time Auterion Suite Fleet Management > Flights.&#x20;

To learn more about how to access and analyze the different log files, please see [Flight Logs](https://app.gitbook.com/s/WXREyAKYAeQJ4gfg2SPg/software/flight-logs).

#### Viewing Logs in Auterion Suite

The easiest way to view the logs is with an [Auterion Suite account](https://docs.auterion.com/vehicle-operation/auterion-sign-up) (Basic version is free).

[Navigate to a particular flight](https://docs.auterion.com/vehicle-operation/auterion-suite-fleet-management/flights) to see many plots showing data such as angles, position, speed, GPS quality, vibration, etc. It will also show the build information, parameter values, and any errors detected in the flight.&#x20;

#### Sharing Flight Logs with Support

To share an uploaded flight log from Auterion Suite, use the "Share with Manufacturer" toggle. This sends the flight log directly to Freefly support. <br>

This creates a support ticket with any information included in the log, statement on submission, and will link to the email associated with Auterion Suite. Be sure to add all relevant details to your submission.

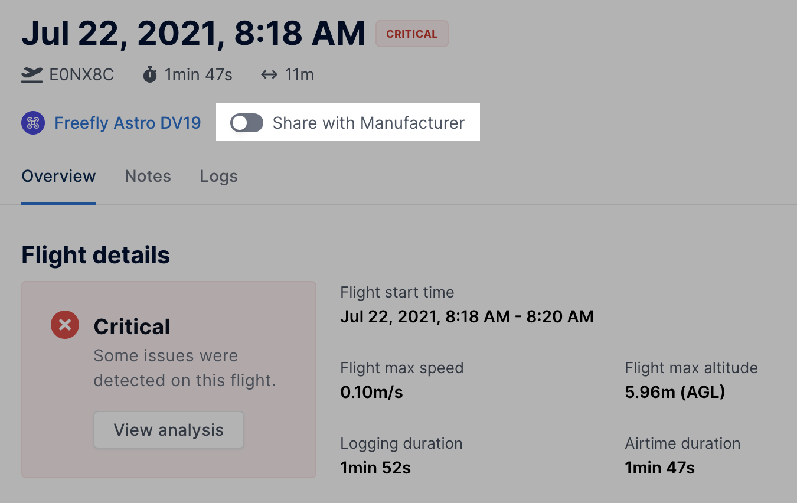
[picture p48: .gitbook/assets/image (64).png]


### Privacy,  Data Sharing, and Security

Freefly believes data generated by Astro, including flight logs, are your property. We think it's important that you are in control of your data, are confident in the measures taken to ensure security, and agree with how the data is used.

The Auterion Privacy Policy gives a layperson's description of how data can flow from Astro, through the Suite, and to partners you choose.

Briefly, when Astro is registered with a Suite account, you can choose to have flight logs automatically uploaded from the aircraft to Auterion servers when an internet connection is available. You can review this data in your Suite account. Auterion employees do not have access to your data. You may choose to share individual flight logs with Freefly Support via the Suite, for example to troubleshoot details of a specific flight.

* Freefly and Auterion understand the need for full data control and user privacy so we have built this platform for maximum user control.
* The Astro comes with hardware to support WIFI and LTE connections to the internet or other devices.
  * If you do not want the LTE to connect, do not install a SIM card for data connection
  * If you do not want the Astro to connect to WIFI, do not select any networks or present any passwords. You can also disable WIFI on the pilot handset.&#x20;
* For security purposes the user needs to have physical access/connection to the Astro in order to register the aircraft to the Auterion Suite because the Auterion Suite enables log uploads, live unit status tracking, live video streaming etc.

{% hint style="info" %}
Learn more about the Astro's internet connections: [wifi](https://freefly.gitbook.io/astro-public/astro/pilots-operating-handbook/network-and-connectivity#wifi) and [LTE](https://freefly.gitbook.io/astro-public/astro/pilots-operating-handbook/network-and-connectivity#lte).
{% endhint %}

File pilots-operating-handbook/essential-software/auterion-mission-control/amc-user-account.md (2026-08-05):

---
hidden: true
---

# AMC - User Account

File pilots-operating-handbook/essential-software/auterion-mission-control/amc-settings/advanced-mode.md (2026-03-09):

# Advanced Mode

By default, AMC hides features, settings, and menus that are not relevant for a drone operator or not intended to be changed by the end user. For development tasks, Auterion Mission Control can be switched into an advanced mode which enables additional menus and features, most notably:

* Analyze Tab -> MAVlink Console
* Analyze Tab -> MAVlink Inspector
* Vehicle Setup Tab

### Enable Advanced Mode in AMC 

In order to switch into the advanced mode, **quickly tap the logo about 7 times** in the top left corner until you are prompted to confirm the change to Advanced Mode.

## MavLink

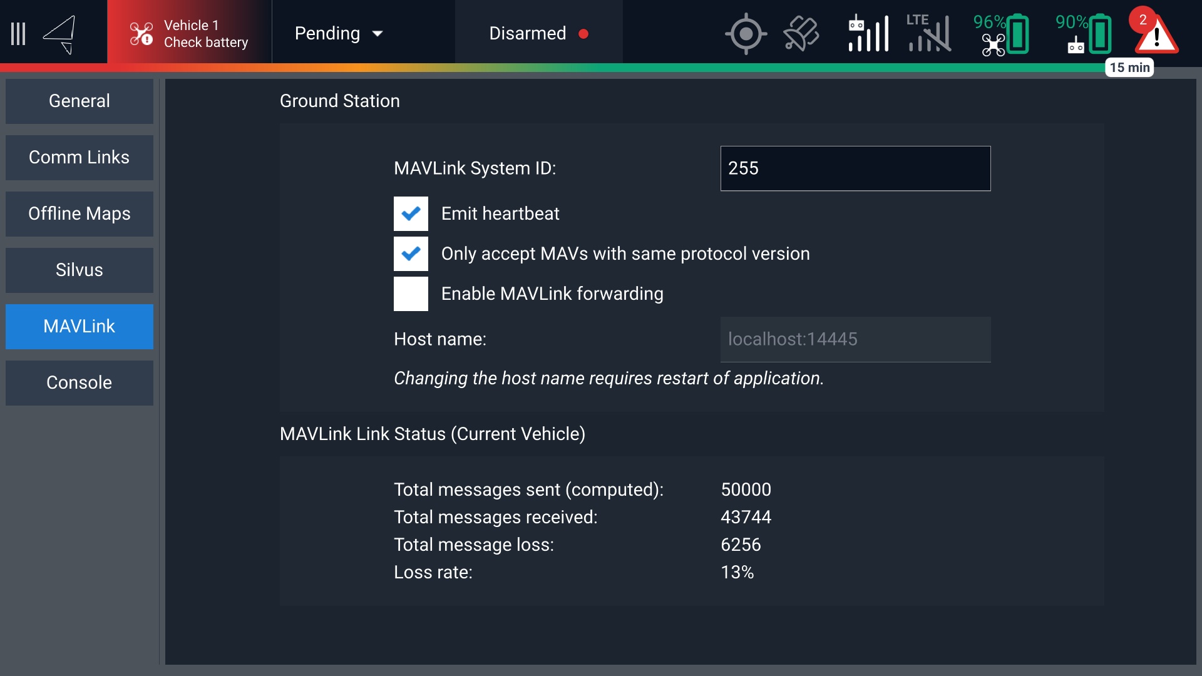
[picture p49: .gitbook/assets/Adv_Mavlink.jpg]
<figure><figcaption></figcaption></figure>

## Console

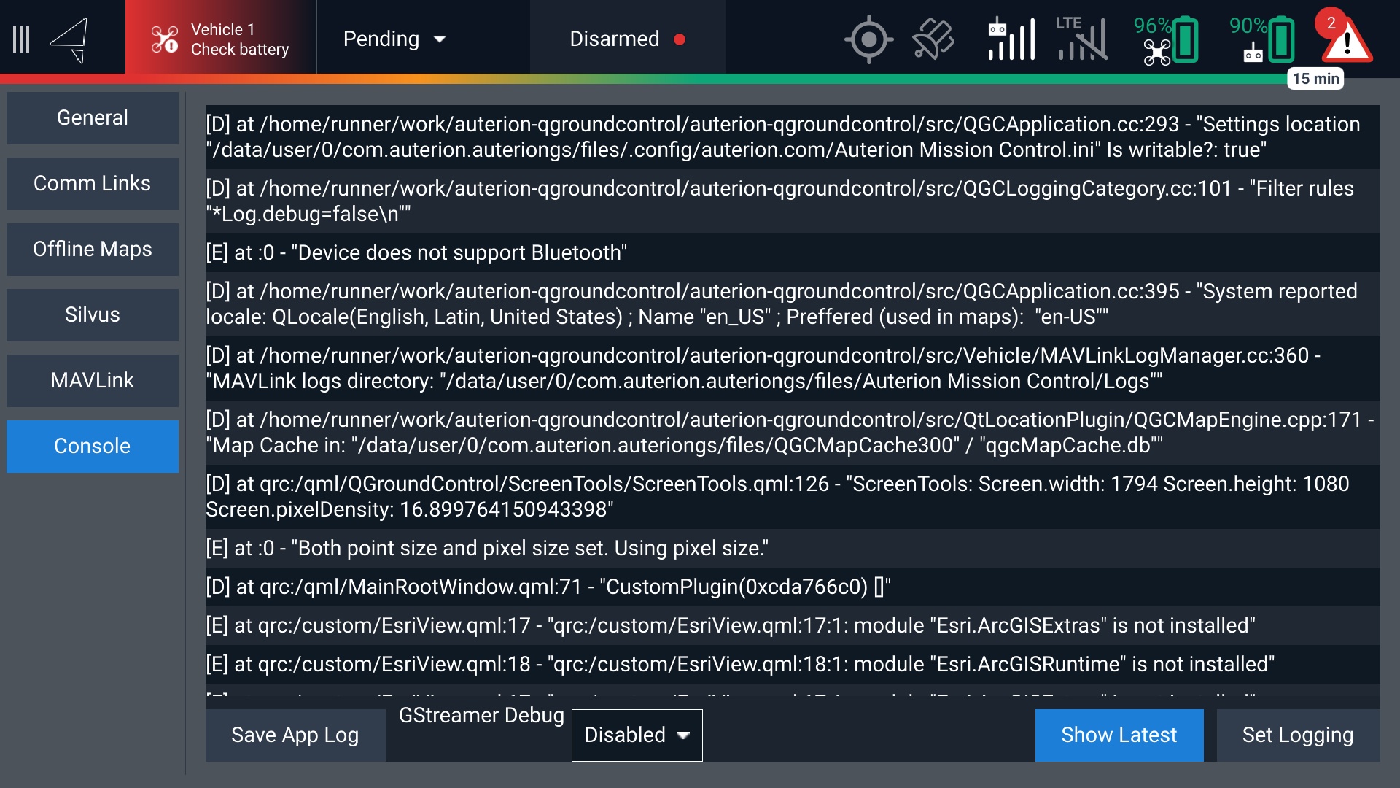
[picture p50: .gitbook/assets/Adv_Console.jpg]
<figure><figcaption></figcaption></figure>

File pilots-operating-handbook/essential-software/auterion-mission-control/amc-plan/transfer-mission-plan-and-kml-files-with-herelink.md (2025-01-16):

# Transfer Mission Plan and KML Files with Herelink

## Options for importing/exporting plans

* **Mission import/export:** AMC’s .plan files can be imported and exported. This is useful for creating missions on a computer, then importing all of them to Herelink at the same time
*   **KML import:** KML files can be imported to AMC. This is useful for creating mission shape definitions in some software, then importing all of them to Herelink at the same time.&#x20;

    Important Note on importing:

    * Zoom in to maximum level, then create a random survey shape. If you don’t zoom in, survey shape could be very large and could crash AMC
    * Then click “import KML” on the right toolbar
    * Survey shape will automatically change to the data defined in the KML import
* **KML export:** This is useful for exporting waypoints outside AMC. You won’t be able to import them back as KML, since these are waypoints, and not a shape definition.

## Procedures for transferring files to/from Herelink

### Method 1: Micro USB port

{% hint style="info" %}
This method may not work as expected on Mac. We recommend using Method 2 on Apple computers.&#x20;
{% endhint %}

1\) Connect the Herelink via the Micro USB port to a computer.

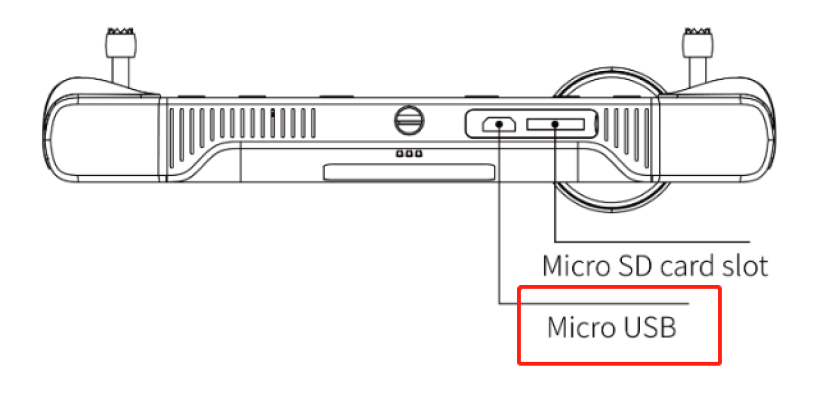
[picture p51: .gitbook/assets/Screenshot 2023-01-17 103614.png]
<figure><figcaption></figcaption></figure>

2\) Turn on the Herelink.

3\) Drag down from the top to open the drop-down menu. Select “USB Charging this device”.&#x20;

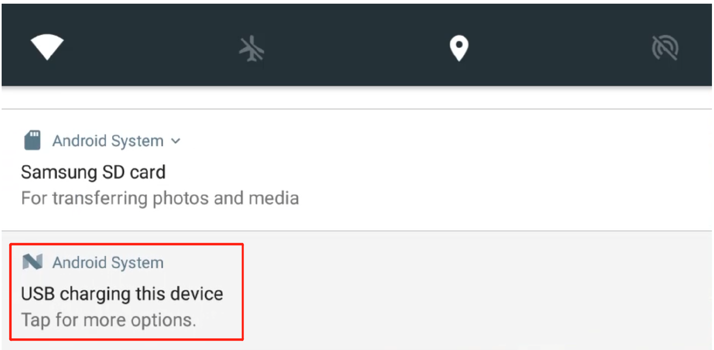
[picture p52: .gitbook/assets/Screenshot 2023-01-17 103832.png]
<figure><figcaption></figcaption></figure>

4\) Select “Transfer files”.

<figure><figcaption></figcaption></figure>

5\) The Herelink will appear on your computer as a device named “Optimus”.&#x20;

<figure><figcaption></figcaption></figure>

6\) Upload flight plans into the following folder: Optimus > Internal shared storage > Documents > Auterion Mission Control > Missions

{% hint style="info" %}
If you aren't seeing the files you're expecting on the Herelink or computer, restart the Herelink.&#x20;
{% endhint %}

### Method 2: Micro SD card (supports maximum 64GB)

1\) Upload flight plans onto the MicroSD card.&#x20;

2\) Insert Micro SD card into the Herelink’s Micro SD Card slot.&#x20;

<figure><figcaption></figcaption></figure>

3\) Drag down from the top to open the drop-down menu and select the Micro SD card device.&#x20;

<figure><figcaption></figcaption></figure>

4\) Select the desired flight plan and select “Copy to…” or “Move to…”\

<figure><figcaption></figcaption></figure>

5\) Select Optimus > Documents > Auterion Mission Control > Missions.&#x20;

<figure><figcaption></figcaption></figure>

6\) Select “Copy” or “Move” to complete transferring.

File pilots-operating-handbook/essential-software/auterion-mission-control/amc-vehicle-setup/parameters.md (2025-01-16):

# Parameters

## Accessing Advanced Parameters

{% hint style="danger" %}
Please exercise extreme caution before changing parameters. Do not operate Astro with edited parameters unless you are certain you know what you're doing or have been instructed to do so by a Freefly employee.&#x20;
{% endhint %}

Parameters are only accessible after [enabling AMC's Advanced Mode](https://freefly.gitbook.io/astro-public/pilots-operating-handbook/essential-software/auterion-mission-control/amc-vehicle-setup/advanced-vehicle-setup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)

{% tabs %}
{% tab title="Video Instructions" %}
{% embed url="https://www.loom.com/share/88cde2426a6145b188512176f82ff53d" %}
Enabling Advanced Mode and accessing parameters
{% endembed %}
{% endtab %}

{% tab title="Text Instructions" %}
1. Enable AMC's advanced mode by rapidly tapping the AMC logo in the top left:
2. A popup to enable Advanced Mode will appear, confirm that you would like to switch to Advanced mode

<figure><figcaption></figcaption></figure>

3. Tap the AMC icon one more time to open the menu, and more options will now appear. Go into Advanced

<figure><figcaption></figcaption></figure>

4. Now scroll down to the bottom and choose Parameters, and parameters will now be accessible and searchable in the screen to the right

<figure><figcaption></figcaption></figure>
{% endtab %}
{% endtabs %}

## Advanced Parameter Commands

### Resetting Parameters to Factory Defaults

On occasion you may need to reset the parameters to the vehicle's default. To do this, once you navigate to parameters, click on Tools > Reset to vehicle's configuration defaults

<figure><figcaption></figcaption></figure>

### Loading Parameter Files

Especially in support situations, we may ask you to load a parameter file. To do this, the file will need to be copied into AMC's visible folder so that it can load the file. AMC will be looking for parameters under Documents > Auterion Mission Control > Parameters

To load the parameter file, go to the parameter page and go to Tools > Load from file. As long as the file is in the right location, it should show up and be selectable to import the parameter changes

<figure><figcaption></figcaption></figure>

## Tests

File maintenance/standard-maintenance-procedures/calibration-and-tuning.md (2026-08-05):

# Calibration and Tuning

## Sensor Calibration

It is not necessary to perform calibrations as a matter of course. Often a calibration will not be required even if the aircraft is relocated a long distance (e.g. by air travel). Compass handling in particular has been improved as compared to past PX4 implementations. For example, shortly after takeoff, the aircraft automatically performs a compass calibration. \
\
In general, sensor calibration should be unnecessary. There are times when it may be required:

* If the magnetic field strength in the operating area is significantly different than where it was calibrated.  If the aircraft appears to have the wrong heading on the ground, makes a large move after takeoff, or flies crooked for a few seconds, those are indicators you should do a compass calibration.
* If the drone has a significant ferrous or magnetic payload installed, it may be required to perform calibration with the payload installed to improve performance.
* If the operating temperature is very hot or cold, it may be required to do a gyro and accelerometer calibration to get best performance. In those cases, power on the aircraft and allow it to sit for 10 minutes in ambient conditions to allow the electronics to warm up, then do gyro and accel cal as directed by AMC. A warning about high accelerometer bias is an indication to do this.
* after doing a full parameter reset, it is usually wise to recalibrate.

Use AMC to calibrate the sensors. [See AMC docs](https://docs.auterion.com/vehicle-operation/settings-and-maintenance/compass-calibration) for the GUI details.

{% hint style="warning" %}
While performing an Accelerometer Calibration, it is best to fold the arms of the Astro and set it down in each orientation. Accelerometer calibration may result in issues if done without placing the drone on a flat surface.&#x20;
{% endhint %}

{% hint style="info" %}
After recalibrating any sensor, make sure to restart Astro before flying. Some changes may not take effect until you reboot the drone.&#x20;
{% endhint %}

## Magnetic Interference

In the event of magnetic interference preventing the aircraft from taking off, follow these [Pro Tips](../../pilots-operating-handbook/limitations.md).

## Tuning

Astro is pre-tuned by Freefly, and can be flown without changes.

{% hint style="warning" %}
We recommend against changing low-level control parameters. Changes there could cause instability or control issues which could result in a crash.
{% endhint %}

{% hint style="info" %}
[Loading default parameters](../software-release-notes/software.md#reset-to-default-astro-parameters) or known-good presets will allow you to quickly return Astro to a functional and safe state if there is ever uncertainty about changes to the tuning properties.
{% endhint %}

Changing low-level parameters requires activating [AMC Advanced Mode](https://freefly.gitbook.io/astro-public/astro/pilots-operating-handbook/software/auterion-mission-control/amc-vehicle-setup/advanced-vehicle-setup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). Then, navigate to Vehicle Setup > Parameters.

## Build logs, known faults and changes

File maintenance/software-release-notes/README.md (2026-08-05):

---
icon: rotate
---

# Software Updates

{% hint style="warning" %}
**#protip** - Verify all Astro components have their software updated together to the latest by referencing the chart below to make sure there are no compatibility issues.
{% endhint %}

## Current Firmware Version

<details>

<summary><strong>Astro v2.2.6</strong></summary>

* **Summary**: New Feature Release. Brings new Boson thermal presets, LR1 and A7R photography improvements, Gremsy VIO plug-and-play, and wide reliability work across flight control, landing, and GPS
* **Release Date**: April 2026
* **Versions in this package**:
  * Astro Skynode: v2.2.6
  * AMC: 1.36.24
  * Pilot Pro App: v2.7
  * Gimbal Firmware: v2.3.0
  * Freefly Updater: v3.1.1
  * LR1 Camera Firmware (recommended): v3.0
* **Notes** (Going from Astro v2.1.x to v2.2.6)
  * **Read more about the highlights** [**here**](astro-software-v2.2-whats-new.md)**!**
  * **Flight**
    * **New:** Mission uploads are now logged into the ulog for customer support and debugging.
    * **New:** Option to disable the emergency battery emergency land behavior.
    * **Fix:** Strong magnetic interference warning wording updated for clarity.
    * **Fix:** Failsafe edge case where user takeover was not possible in the fallback Land action when the configured RTL was not possible.
    * **Fix:** Altitude no longer changes when switching between manual and position modes in some edge cases.&#x20;
    * **Fix:** Distance sensor fog check improvements.&#x20;
    * **Fix:** Improved landing reliability.&#x20;
    * **Fix:** Log cleanup now runs reliably on all drones.
    * **Fix:** Improved GPS reliability. Mitigates the known issue in [Astro SB012](https://freeflysystems.com/knowledge-base/astro-sb012-astro-software-v2-1-13-addresses-service-bulletins-sb010-and-sb011).
  * **Payload**
    * **New:** LR1 and A7R Fixed Focus mode. Locks the camera at the current focus distance without re-racking, ideal after tap-to-focus for near subjects.
    * **Fix:** Blurry Infinity Focus on certain Sigma 24mm lens versions (v.03 firmware). The payload driver now reads lens firmware version and applies the correct focus offset per version, on both LR1 and A7R.
    * **New:** LR1 and A7R RAW and RAW+JPEG image format support. RAW images save to the camera SD card only.
    * **New:** Gremsy VIO is now plug-and-play. Swapping between an LR1 and a VIO no longer requires parameter changes. VIO must be configured correctly or purchased from Freefly. If using VIO geotagging, the MAVLink mode must be changed, which removes the blue configuration of the aircraft.
    * **New:** Boson Wildfire Contrast Preset, pre-configured for wildfire detection with advanced contrast and isotherm defaults.
    * **New:** Simplified Isotherm views for Boson. "Temp Above" and "Temp Below" each expose a single isotherm band, making it easier to highlight the hottest or coldest objects.
    * **New:** Advanced Contrast Settings for Boson are now in a separate dropdown. Switching Contrast Preset resets Advanced Contrast Settings to the new preset's values.
    * **Fix:** Boson radiometric TIFF captures are now significantly faster.
    * **Fix (AMC):** Flir Boson+ 640 added to available camera profiles.
    * **New:** LR1 APS-C crop support in video mode. Requires LR1 camera firmware newer than v1.0.0.
    * **New:** LR1 additional video recording formats, including XAVC S-I 4K.
    * **Fix (AMC):** Flux survey planning improvements.
  * **Pilot Pro**
    * **New:** RTK and NTRIP can now be run from Pilot Pro on MAVLink-over-ethernet vehicles.
    * **New:** Doodle radio channel scan now scores channels by airtime activity, not just noise, with visual bars and per-channel diagnostics.
    * **New:** Customizable Pilot Pro Status page for integrators.
    * **New:** Pilot Pro now always verifies all input-output parameters to ensure the applied config matches controller state.
    * **Improvement:** Android battery optimization configured so critical Freefly apps are not killed when backgrounded.
    * **Improvement:** Graceful tablet shutdown so Android settings persist across boot.
    * **Improvement:** Software update UX.
    * **Improvement:** Better vehicle and serial connection state management.
    * **Fix:** Log pruning is now capped at 3 GB.
    * **Fix (Freefly Updater):** Auto-fetch on app start now works reliably.
    * **New (Freefly Updater):** Pop-up warning when there is no internet connectivity.

</details>

### Latest Versions

<table data-full-width="true" data-search="false"><thead><tr><th width="221">Component</th><th width="248">Current Compatible Versions</th><th width="245">How To Update</th></tr></thead><tbody><tr><td><strong>Astro</strong></td><td></td><td></td></tr><tr><td>Software</td><td><strong>2.2</strong>.6</td><td><a href="software.md#updating-astro-firmware">Astro Firmware</a></td></tr><tr><td>SL8 Battery</td><td>2.1, 1.10, or 1.9</td><td><a href="https://docs.freeflysystems.com/ecosystem/power/superlight-batteries/firmware-updates">Battery Firmware</a></td></tr><tr><td><strong>Pilot Pro</strong></td><td></td><td></td></tr><tr><td>Pilot Pro Firmware</td><td><strong>2.2</strong>.0</td><td><a href="https://freefly.gitbook.io/pilot-pro-public/maintenance/software-and-firmware-updates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">Update</a> through the Pilot Pro App</td></tr><tr><td>Pilot Pro App</td><td><strong>2.7</strong>.8</td><td>Check the <a href="https://freefly.gitbook.io/pilot-pro-public/maintenance/software-and-firmware-updates#app-updates">"updates"</a> section in Updater app</td></tr><tr><td>AMC App</td><td><strong>1.36</strong>.24</td><td>Check the <a href="https://freefly.gitbook.io/pilot-pro-public/maintenance/software-and-firmware-updates#app-updates">"updates"</a> section in Updater app. Desktop versions can be downloaded <a href="https://freeflysystems.com/support/astro-support">here</a>.</td></tr><tr><td>Freefly Updater App</td><td>3.1.1</td><td>Check the <a href="https://freefly.gitbook.io/pilot-pro-public/maintenance/software-and-firmware-updates#app-updates">"updates"</a> section in Updater app</td></tr><tr><td><strong>Herelink GCS (Legacy)</strong></td><td></td><td></td></tr><tr><td>OEM</td><td>FFARU01231123</td><td><a href="../../other-user-manuals/ecosystem/components/pilot-handsets/herelink-controller-maintenance/updating-herelink-software.md">Herelink Firmware</a></td></tr><tr><td>AMC App</td><td><strong>1.36</strong>.24</td><td>Check the updates section in the Updater app</td></tr><tr><td><strong>Payloads</strong></td><td></td><td></td></tr><tr><td>Freefly Payloads (LR1, A7R4, OGI, Wiris Pro)</td><td><a href="https://app.gitbook.com/s/WXREyAKYAeQJ4gfg2SPg/payloads">See payloads page</a></td><td><a href="https://app.gitbook.com/s/WXREyAKYAeQJ4gfg2SPg/payloads/payload-maintenance/gimbal-firmware">Gimbal Firmware</a></td></tr><tr><td>Hovermap ST/ST-X</td><td><a href="https://app.gitbook.com/s/WXREyAKYAeQJ4gfg2SPg/payloads/third-party-payloads/hovermap-st-x-and-st-lidar">Latest supported version</a></td><td><a href="https://knowledge.emesent.com/">Update Hovermap</a></td></tr><tr><td>Sentera 6X and 65R</td><td><a href="https://app.gitbook.com/s/WXREyAKYAeQJ4gfg2SPg/payloads/third-party-payloads/sentera-6x-65r">Latest supported version</a></td><td><p><a href="https://sentera.gitbook.io/65r-sensor-user-guide">65R User Guide</a></p><p><a href="https://sentera.gitbook.io/6x-multispectral-sensor-user-guide">6X User Guide</a></p></td></tr><tr><td>Gremsy VIO</td><td><a href="https://app.gitbook.com/s/WXREyAKYAeQJ4gfg2SPg/payloads/third-party-payloads/gremsy-vio">Latest supported version</a></td><td><a href="https://docs.gremsy.com/payloads/vio">VIO Wiki</a></td></tr><tr><td>Gremsy Pixy PE</td><td><a href="https://app.gitbook.com/s/WXREyAKYAeQJ4gfg2SPg/payloads/third-party-payloads/gremsy-pixy-pe">Latest supported version</a></td><td><a href="https://docs.gremsy.com/pixy-and-mio/pixy-u">Update Pixy</a></td></tr><tr><td>Flux Lidar</td><td><a href="https://app.gitbook.com/s/WXREyAKYAeQJ4gfg2SPg/payloads/flux-lidar">Latest supported version</a></td><td><a href="https://freefly.gitbook.io/astro-public/other-user-manuals/freefly-payloads/flux-lidar-payload/flux-software">Update Flux software</a></td></tr></tbody></table>

***

## Previous Firmware Versions

### Astro v2.1 Release Notes

<details>

<summary>Astro v2.1.13</summary>

* **Summary**: Hotfix release addressing issues in SB010 and SB011
* **Release Date**: September 2025
* **Versions in this package**:
  * Astro Skynode: v2.1.13
  * AMC: 1.36.21
* **Notes**
  * Fixed: [Astro Service Bulletin 011](https://freeflysystems.com/knowledge-base/astro-sb011) by correcting serial communication between the Skynode and PX4.
  * Fixed: [Astro Service Bulletin 010](https://freeflysystems.com/knowledge-base/astro-sb010) with the following changes:
    * Adjusted GNSS checks after initial 3D fix; continue GNSS fusion if a single metric degrades (e.g., high DOP) while other metrics remain nominal.
    * Use PX4 default u-blox multirotor (<2 g) GNSS dynamic model.
    * Enable a stricter PDOP check.
  * New: FF\_INPUT\_TYPE parameter simplifies the controller setup. This can be set in AMC > Vehicle Menu > Select Controller.
  * New: Herelink radios can be bound using the IO-panel bind button on Astro—no need to open the radio enclosure.
* **Known issue: RTK/NTRIP bursts can briefly drop GPS-assisted modes.** Sudden, buffered RTCM corrections can delay GNSS processing for a few seconds, temporarily exiting Position/Auto/RTL. **Applies to:** all currently released firmware, only when RTK or NTRIP is being used. Mitigations:
  * **If you need RTK/NTRIP**: set GPS\_DUMP\_COMM = Disabled (0) in AMC in [advanced mode](https://freefly.gitbook.io/astro-public/pilots-operating-handbook/essential-software/auterion-mission-control/amc-vehicle-setup/parameters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) → Parameters. This limits GPS output so correction bursts cannot overrun processing. **Note**: while set to Disabled, **PPK** workflows are unavailable—restore this parameter to default when you need PPK.
  * **Status**: Fix in progress for a follow-up patch.

</details>

### Astro v2.0 Release Notes

<details>

<summary>Astro v2.0.22</summary>

* **Summary**: Minor update to v2.0.19
* **Release Date**: August 2025
* **Versions in this package**:
  * Astro Skynode: v2.0.22
  * AMC: 1.34.21
*   **Notes**

    Astro v2.0.19 -> v2.0.22

    * **New**: Herelink radio binding can now be initiated with the bind button on Astro’s IO port. This removes the need for removing the radio’s enclosure to access the bind button on the Herelink itself.
    * **Fix**: Sony 50mm F1.8 lens above F5.6 on LR1 and A7RIV had issues with autofocus delays, causing missed captures and out of focus images. This is now fixed in Astro software.
    * **New**: Added support for Sony FE 50mm F2.5 G lens on LR1 Payload
      * Requires LR1 gimbal firmware 2.2.0 or later
* **Known Issues**
  * Service Bulletin freeflysystems.com/knowledge-base/astro-sb010
  * Service Bulletin freeflysystems.com/knowledge-base/astro-sb011
  * The time until the RTL indicator bar displayed at the top of the Fly view in AMC is sometimes inaccurate.
  * Changing some parameters require reboots, but the reboot prompt isn't displayed. It is best practice to always reboot after changing parameters.

</details>

<details>

<summary>Astro v2.0.19</summary>

* **Summary**: Major PX4 upgrade from v1.13 to v1.15
* **Release Date**: May 2025
* **Versions in this package**:
  * Astro Skynode: v2.0.19
  * AMC: 1.34.21
* **Notes (**&#x41;stro v1.9 -> v2.0
  * **Read more about the highlights** [**here**](astro-software-v2.0-whats-new.md)**!**
  * **Operational Behavior Changes**
    * **Astro now boots in Position Flight Mode** - In previous versions of Astro firmware, the aircraft would boot up in 'Pending' flight mode while waiting for the required GPS satellites and position accuracy metrics. With 2.0 Astro firmware, the aircraft now boots up in Position mode, but displays 'No valid position estimate' until the satellite counts and position accuracy metrics are met.
    * **Astro can re-arm after using the kill switch -** In previous versions of Astro firmware, it was not possible to re-arm the aircraft after the kill switch was used without an aircraft reboot. With the 2.0 firmware release, it is now possible to reset the kill switch position and then re-arm Astro without a reboot of the aircraft. Make sure to update your pilot pro firmware to version 2.0 as well!
  * **New: Gimbal Snap to 0, 45, 90 Degrees** - In AMC 1.34 under Controller > Joystick > Button Configuration, the following actions are now functional and can be mapped to buttons or switches on the GCS: Gimbal Center, Gimbal Pitch 45, Gimbal Pitch 90.
  * **New: Gimbal Direct Control** - We've pulled in some code from our Movi Pro ecosystem to improve gimbal yaw smoothness for Freefly Payloads! In Astro 2.0 firmware when flying in Position Slow mode, the aircraft now follows the heading of the gimbal for more precise and cinematic shots. This feature is available for LR1/A7R4/Wiris Pro/OGI payloads. Info on configuring gimbal expo/window/smoothness is [here](https://freefly.gitbook.io/astro-public/other-user-manuals/freefly-payloads/workflows-maintenance-updates/precise-smooth-gimbal-control).
  * **New: LR1/A7R4 Intervalometer mode** - This can be toggled under the LR1/A7R4 camera settings: Settings > Enable Interval Shooting, Set trigger interval, Press shutter button to start and stop. (If you are saving images to the USB stick, we recommend a minimum trigger interval of 2.0s or greater. If you need to go faster than this, set your storage mode to SD card).
  * **New: Georeferenced PDF import in AMC** - In AMC 1.34, georeferenced PDF maps can now be imported and overlaid on the primary map.
  * **New**: Astro’s base PX4 version has been upgraded from v1.13 to v1.15.
  * **New**: Integrated Freefly Doodle FW v1.7 in Pilot Pro App. This allows updating v1.4 units to the latest. Additionally, any radio pair that is on v1.7 now benefits from faster pairing and channel changes.
  * **New**: Enabled native screen mirroring in Pilot Pro from the tablet to an external display.
  * **Fixes and Improvements:**
    * Improved vertical accuracy in geotagged photos.
    * Improved Thermal Module Temperature Display - New graphics overlay to clearly display the temperature readout when using spot metering.
    * Added gimbal version compatibility checks in AMC.
    * Improved GPS reliability
      * Reduced GPS output rate to increase reliability.
      * Enabled BeiDou.
    * Wifi configuration
      * Fixed a bug where sometimes the 'connect' button is greyed out.
      * Nearby network names are now shown.
    * Fixed an issue where Astro could unexpectedly move when transitioning from Manual --> Position mode
    * Integrator notes:
      * COM\_OBL\_ACT was removed/merged to COM\_OBL\_RC\_ACT.
      * Added ability to disable IMU1 for CPU reduction.
* **Known Issues**
  * The time until the RTL indicator bar displayed at the top of the Fly view in AMC is sometimes inaccurate.
  * Changing some parameters require reboots, but the reboot prompt isn't displayed. It is best practice to always reboot after changing parameters.

</details>

### Astro v1.9 Release Notes

<details>

<summary>Astro v1.9.2</summary>

* **Summary**: Introduces Astro Max and Freefly OGI Payload
* **Release Date**: January 2025
* **Versions in this package**:
  * Astro Skynode: v1.9.2
  * AMC: 1.33.11
*   **Notes**

    Astro v1.7 -> v1.9

    * New: Freefly OGI Payload support
    * Fix: Adds GPS tagging from GPS altitude. This is a patch to improve height accuracy in RTK tagged images.
    * Fix: Remove button mapping fltmode5 = -1. It was causing issues if the assigned channel was active.
    * Fix (going from v1.9.1 to v1.9.2): Freefly has identified an issue in Astro Max firmware v1.9.1 where the system may fail to detect landing and thus not disarm. v1.9.2 has a parameter value update to correct this issue.

    <br>

    AMC v1.32.7 -> v1.33.11

    * New: Freefly OGI Payload support
      * Adds custom camera actions 1-3
      * Custom camera action 1 is mapped to GEM on/off.

</details>

### Astro v1.7 Release Notes

<details>

<summary>Astro v1.7.2</summary>

* **Summary**: Introduces integration for LR1 Thermal Module \[Boson 640R], and various improvements
* **Release Date**: September 2024
* **Versions in this package**:
  * Astro Skynode: v1.7.2
  * AMC: 1.32.7
* **Notes**
  * **Read more about the highlights** [**here**](astro-software-v1.7-whats-new.md)
  * New: Integrated LR1 Thermal Module \[Boson 640R]. Includes spot metering and digital zoom up to 8x
  * New: Digital Zoom 1.0 to 4.0x digital zoom on LR1 and A7R4 Payloads for live preview and saved images/videos.
  * New: Tap to Focus for LR1 and A7R Payloads
  * New: Payload zoom on Pilot Pro right side rocker. Zoom function is now mapped to the right hand rocker (below R1 button) on Pilot Pro. This works for LR1 Payload, AR4 Payload, Thermal Module for LR1, Wiris Pro Payload
  * Fixes and Improvements:
    * LR1 Payload - Fixed an overheat condition on bootup
    * LR1 Payload - Fixed soft focus in infinity focus mode
    * A7R4 Payload - Removed incorrect 50mm infinity focus setting
    * AMC - Removed Structure Scan
    * AMC - LR1 and Thermal Module appear as EO/IR toggle when both connected
    * Distance Sensor Module - can now select between ft. and meters
    * Distance Sensor Module - displays +99m when max range is reached
    * Added support for up to 3 cameras on Astro
* **Known Issues:**
  * Slow Mode's zoom rate scaling requires reinstallation. To enable it again, go to 10.41.1.1 Astro settings, find installed applications, and press the settings button on the Slow Mode app to initialize it.
  * Currently, video can only be recorded on LR1 and one additional camera (ex: LR1 and Thermal) simultaneously. Wiris Pro is treated in the software as one camera

</details>

### Astro v1.6 Release Notes

<details>

<summary>Astro v1.6.14</summary>

* **Summary**: Support for Astro Prime, Blue, and LR1 Payload
* **Release Date**: July 2024
* **Package version number**: v1.6

**What's New**

* Integration with Freefly’s **Doodle radio modules**, an NDAA and Blue approved radio module.
  * Freefly built firmware with optimized configurations for real-world Astro flights.
  * Pairing Manager
  * Channel change settings
  * Logging option
  * Firmware updates
  * Option to enable RJ45
* Blue Security features that make Astro an approved[ Blue UAS](https://www.diu.mil/blue-uas-cleared-list)
  * Ability to enable/disable individual security features.
  * • Ability to add multi-user authentication for admins.
  * Stealth logging option that removes positional information from logs. (Please note that having this mode turned on will conflict with PPK mapping workflow)
* Mapping and Mission
  * Metadata updates:
    * See the latest version [here](https://docs.google.com/spreadsheets/d/1xIpZqTWhw0xUHtjHwL9-C6rHBFWwdkcftMq3vk0WBdo/edit?usp=sharing)
    * Added coordinate system to JPEG XMP metadata.
    * Added use of UTC time for date and time in Exif metadata.
    * Added RTK accuracy tag to XMP.
    * Fixed camera attitude in XMP tags.
    * Moved from DJI to Pixhawk XMP block. **This is important to note for mapping workflows**
  * Improved error handling when USB storage is disconnected.
  * PPK processing stability improvements.
  * New mission manager menu for integration with Auterion Suite Mission Sync.
  * Increased Corridor Scan max width to 500m.
* Payload
  * Integration with Freefly’s new Sony LR1 payload
    * Advanced payload parameters in AMC
    * Automatic tuning profiles based on detected lens.
  * Video recording settings for A7R and LR1 payloads.
  * Added JPEG quality setting options to the menu.
  * Fixed the gimbal angles display in AMC.
  * AMC now displays payload gimbal firmware version number.
  * Fixed gimbal tilt drift caused by AMC
* Exposed the option to set COM\_RC\_OVERRIDE behavior in AMC safety tab. When this setting is enabled moving the RC sticks immediately gives control back to the pilot by automatically switching to Position mode and if position is unavailable, then to Altitude mode.

**Known Issues**

* **A7R4 and Wiris payloads** need their gimbal firmware updated to v1.7 or above. Not doing so will result in compatibility issues in performance.
*   **Hovermap ST-X payload** requires two parameter changes to work with 1.6 FW.

    * Set MAV\_2\_MODE = Normal
    * Set COM\_RC\_IN\_MODE = RC Transmitter Only

    Hovermap is not yet compatible with Astro Blue/Doodle variant.

</details>

### Astro v1.5 Compatibility Table

<table data-full-width="false"><thead><tr><th width="221">Component</th><th width="285">Current Compatible Versions</th></tr></thead><tbody><tr><td><strong>Astro</strong></td><td></td></tr><tr><td>Software</td><td><strong>1.5</strong>.18</td></tr><tr><td>SL8 Battery</td><td><strong>1.10</strong> or 1.9</td></tr><tr><td><strong>Pilot Pro</strong></td><td></td></tr><tr><td>Firmware</td><td><strong>1.1</strong>.4</td></tr><tr><td>App</td><td><strong>1.1</strong>.11</td></tr><tr><td>AMC App</td><td><strong>1.26</strong>.15</td></tr><tr><td>Herelink GCS (Legacy)</td><td></td></tr><tr><td>OEM</td><td>FFARU01231123</td></tr><tr><td>AMC App</td><td><strong>1.26</strong>.15</td></tr><tr><td><strong>Payloads</strong></td><td></td></tr><tr><td>A7R4</td><td><strong>1.6</strong>.2</td></tr><tr><td>Wiris Pro</td><td><strong>1.6</strong>.2</td></tr><tr><td>Hovermap</td><td></td></tr><tr><td>Sentera</td><td></td></tr></tbody></table>

<details>

<summary>Astro v1.5.18</summary>

* **Summary**: Remote ID Support, Astro FPV integration, ESRI Site Scan and other bugfixes
* **Release Date**: March 2024
* **Versions in this package**:
  * Astro Skynode: v1.5.18
  * AMC (Android): v1.26.15
* **Notes**
  * New: [Standard Remote ID Integration](../../other-user-manuals/compliance/faa-remote-identification-rid.md)
  * New: [Astro FPV Support](https://store.freeflysystems.com/products/optional-fpv-system-for-astro)
  * New: Added [Sentera 6X and 65R](https://freeflysystems.com/payloads) options to AMC
  * ESRI Site Scan is now compatible with Astro v1.5 and above
  * Mission and Surveying Fixes:
    * Fixed a bug in the execution of missions with altitude changes. There was an issue with aircraft not always following the intended vertical flight trajectory between waypoints.
    * Fixed a bug where geotagged altitudes could be wrong when using a USB camera
    * Improved the Sony A7RIV triggering consistency during surveys. The jitter between triggers is now significantly reduced
    * Improved RTK geotagging. Previously, the vehicle's location was used to geotag images onboard the vehicle. Although the PPK workflow corrects for any shift during post-processing, accurate RTK geotagging must occur onboard for optimal precision.
    * Improved the speed in generating the necessary onboard PPK files by over 3 times
    * Fixed an issue with PPK process writing the same capture event twice in the Rinex file
    * Fixed issue that would cause the PPK status in AMC to be incorrect. In some cases the processing popup would never show up while in other cases it would show up but never go away
    * Fixed the 200 feet constrain on corridor width limit
    * **Known issue:** Site Scan Reality Engine does not correctly process the gimbal attitude, resulting in poor output maps. [Current workaround](https://freefly.gitbook.io/astro-public/other-user-manuals/payloads/a7r4-mapping-payload/operating-handbook/pro-tips) is to use the Legacy Engine
  * More
    * Optimized video streaming to the GCS by reducing the number of data spikes over the radio link
    * Added VEHICLE\_MANUFACTURER and MODEL for XMP metadata for easy ingestion by Trimble Business Center
    * Updated max yaw rate to 75 deg/s for more precise control
    * Added a guard to battery emergency logic. If a battery reports a sudden jump to 0% state of charge, Astro will do additional checks to see if this might be a faulty report, then it will initiate an RTL instead of a direct Land action.
    * Fixed and issue where slow mode intermittently using wrong camera for scaling
    * Improved data usage by not uploading photos to the suite that are taken while the drone is disarmed
    * Optimized photo storage on external USB stick. Depending on the usb stick write speed there could be situations where the photo storage would slow down the rest of the payload operations.
    * Fixed an issue that would cause the payload to never be detected after a brief payload disconnection
    * Added ability to center map on vehicle, on payload Center Field of View or both
    * Added software compatibility check between AMC and AuterionOS

</details>

<details>

<summary>Astro v1.4.6</summary>

* **Summary**: Introduces the Pilot Pro integration
* **Release Date**: November 2023
* **Versions in this package**:
  * Astro Skynode: v1.4.6
* **Notes**
  * **Read more about the highlights** [**here**](astro-software-v1.4-whats-new.md)
  * New: Pilot Pro Integration
  * New: Velocity Control (aka Slow Speed Mode)
  * Operational Behavior Changes
  * Herelink GCS Updates
  * User Interface (UI) Enhancements
  * Status and Monitoring Improvements
  * Photo Gallery Updates
  * Mapping and Mission Planning Updates
  * Auterion Suite Integration Updates
  * Fixes and Improvements
* **Known Issues:**
  * ESRI Site Scan Flight for ArcGIS is not supported with this software bundle.
* **Important Note** for Herelink users -> [switching-to-freefly-updater.md](../../other-user-manuals/ecosystem/components/pilot-handsets/herelink-controller-maintenance/switching-to-freefly-updater.md "mention")

</details>

<details>

<summary>Astro v1.3.2</summary>

* **Summary**: Astro Software release that introduces the Wiris payload integration
* **Release Date**: June 2023
* **Versions in this package**:
  * Astro Skynode: v1.3.2
    * Herelink OEM build number: FFARU01230623
* **Notes**
  * **Introducing the Wiris Payload Integration.** [Read the manual here!](/broken/pages/SWbzoab49OlVarm4Mr1J)
  * New service provider for terrain follow with v1.17.18. (AMC v1.17.17 or earlier will no longer have the terrain follow working starting July 2023)
  * Bugfix for a rare issue where orbit start commands would get delayed for multiple minutes
* **Known Issues:**
  * Herelink suggests that you should update the Air unit as well. However you don't need to update the air unit.
  * ESRI Site Scan Flight for ArcGIS soon to add support for this firmware

</details>

<details>

<summary>Astro v1.2.10</summary>

* **Summary**: Major Astro Software release that includes new Compassless flight mode, and dozens of new features and improvements
* **Release Date**: May 2023
* **Versions in this package**:
  * Astro Skynode: v1.2.10
  * Herelink OEM build number: FFSRU01230515
* **Known Issues:**
  * v1.2.10 may display itself as v1.2.9 in AMC or in the Auterion Suite
  * Herelink suggests that you should update the Air unit as well. However, you don't need to update the air unit.
  * ESRI Site Scan Flight for ArcGIS soon to add support for this firmware
  * AMC Photo Gallery doesn't always load. This will be fixed soon

**Download** [**here**](https://drive.google.com/file/d/1Qp3qI54sjc3dEn-yHZDAYMRWuPZuaeQ3/view)

**Read more about the highlights** [**here**](astro-software-v1.2-whats-new.md)

</details>

<details>

<summary>Astro v1.1.18</summary>

* **Summary**: Several hotfixes that address safety critical issues
* **Release Date**: February 2023
* **Versions in this package**:
  * Astro Skynode: v1.1.18
  * Herelink OEM build number: FFARU010624

**Notes**

* **Several hotfixes that address SD Card driver and priority issues that caused an Astro to crash**
  * Hotfixed SD Card driver to eliminate a possible hang when the SD card is disconnected during a wait for write to complete. This was the initial cause of the crash that triggered grounding
  * Removed PX4’s emergency logger priority boost mechanism which could hang the system if the logger or log\_writer thread was already hung (possibly due to the above issue). This priority boost is what promoted the stuck logging thread to max priority, with the intent of capturing what was wrong, but instead caused the processor to hang in the high priority loop.
  * Increase semaphore holder slots so that there is no situation where it could run out during a resource contention. This can happen during shutdown where multiple modules write parameters at the same time.
  * Hotfixed px4io module to ensure DMA is properly closed and restarted in case of a transfer failure
  * Hotfixed px4io module to ensure that in case of corrupted SBUS data, the input processor can’t try and process more than the valid data
* **Hotfix for GPS dropouts affecting Astro functionality**
  * Default GPS configuration now disables Beidou constellation processing on the F9P GPS. There is a suspected weakness in the GPS firmware where bad SBAS data may cause added CPU load on the GPS and it becomes overloaded, which may cause GPS lock to drop for a few seconds.
* **Known issue:** During testing, a Freefly Engineering aircraft failed to fully complete the disarm process. The motors shutdown, but the system hung. This has happened 3 times to this specific aircraft, including on older firmware. It is still being investigated, but we don’t believe this was added in this firmware. It has only happened to one vehicle, and failed safely each time.
* **Testing for this release included**
  * Hotfix specific test plan for the new changes
  * Full software validation testing
  * 50+ hours of functional flight time across over 10 pilots and Astros

**Read more details** [here](https://docs.google.com/document/d/1FyLmrl8n_S8AF9IlVJMZwn4WO1uzZpPA2jt0hxa9zwM/edit#heading=h.bf7erfhck8fc)

</details>

<details>

<summary>Astro v1.1.14</summary>

* **Summary**: Introducting ESRI Site Scan for ArcGIS integration
* **Release Date**: September 2022
* **Versions in this package**:
  * Astro Skynode: v1.1.14
  * Herelink OEM build number: FFARU010624

**Notes**

* **New Feature:** Integration with ESRI Site Scan for ArcGIS!
  * Complete solution - Freefly Astro integrated with Site Scan for ArcGIS provides a complete end-to-end drone mapping solution. From drone hardware, automated flight planning and execution, online and offline, to imagery processing on the cloud or on desktop, to advanced analysis in ArcGIS…
* **New Feature:** ExFat support. You can now use USB drives with any memory size, and format them using a Windows computer. Simply select ExFat format.
* **Improvement:** auterionOS and AMC now uses a global counter for the pictures taken
* **Bugfix:** Fixed the camera pre-flight check fails

</details>

<details>

<summary>Astro v1.1.11</summary>

* **Summary**: Astro Map initial release
* **Release Date**: May 2022
* **Versions in this package**:
  * Astro Skynode: v1.1.11
  * Herelink OEM build number: FFARU01220425

**Notes**

* **Operational Behavior Changes**
  * **New Feature - Failsafe change**: Before executing critical and emergency battery failsafes, Astro now switches to “hold” mode for 10 seconds and shows an alert on the AMC. This allows the pilot to have an opportunity to take any manual action, such as aborting the RTL incase vehicle is operating below obstacles. RTL can be be cancelled by selecting any other flight mode.
  * **New Feature - Initial mode behavior change**: Astro will now boot into PENDING mode, and will transition to Position mode when GPS accuracy requirements are met. This prevents accidentally taking off before the Position mode is available and being confused as to why position hold and RTL failsafe is unavailable. If the pilot wants to takeoff before this (without GPS), they can switch to Altitude or Manual mode.
  * New Feature: Astro will now go through a 3 stage landing for a smoother touchdown. This autoland is available within 50m horizontally and 30m vertically from the takeoff location. Outside of these bounds, Astro will autoland using the 2 stage touchdown, as it did in v1.0.21.
  * Improvement: Mission pause and resume actions will resume the mission from the last completed waypoint
  * Improvement: Mission and cruise speed defaults are set to 10 m/s
  * Improvement: Default mission altitude is set to 50m
* **System and Other Changes**
  * New Feature: Astro will now GPS geotag the photos with high accuracy and move them any attached USB storage device. High accuracy is achieved with the integration of camera hotshoe signals, and 1PPS time synchronization
  * New Feature: Astro will automatically write GPS observation files to any attached USB storage device at end of flight for use in PPK processing of flight path or photos. If the aircraft is powered off before observation file writing is complete, it will be placed in a recovery folder on the USB drive at next boot.
  * New Feature: Herelink runs an additional app (Skyway) to route telemetry and video to hotspot devices. This allows connection of multiple devices to Herelink hotspot and stream data and video from Astro
  * Improvement: Astro prevents flashing non-Astro firmware releases to Skynode
  * Improvement: Astro requires a magnetometer calibration after firmware update and parameter reset
* **AMC Changes**
  * New Feature: AMC will display estimated flight time remaining in minutes as a bar at the top of the screen
  * New Feature: Herelink radio signal strength indicator in status bar
  * New Feature: Support for Astro Map system
  * New Feature: Progress indicator after landing to let users know when GPS observations are done processing. You can set aircraft parameter GPS\_DUMP=0 to silence this notification (which will also disable writing data necessary for PPK processing).
  * Improvement: AMC now runs in background. Minimizing AMC app won’t trigger datalink failsafe
  * Improvement: Auterion suite pilot login
  * Improvement: Terrain collision calculations are improved when planning a mission
  * Improvement: UI for maximizing video window is improved
  * Bugfix: Performance impact of capturing hundreds of photos during a survey is reduced
  * Bugfix: Corridor scan will now trigger photos on all flight legs
* **Developer/advanced user Changes**
  * New Feature: 1PPS pulse is available on the IO board ZPD connector
  * New Feature: Support for Mavlink Gimbal protocol V2 - [https://mavlink.io/en/services/gimbal\_v2.html](https://mavlink.io/en/services/gimbal_v2.html)
  * New Feature: Camera trigger and feedback is enabled
  * Improvement: External serial port is renamed from TELEM4 to PPB. Baud is now configured with SER\_PPB\_BAUD. Default baud rate is now 921600
  * Improvement: Astro now requires Smart batteries with firmware v1.9 and above (this should only impact beta testers, v1.9 was the initial public battery release firmware).
* **More Details**
  * Astro v1.1.11 is based on AuterionOS 2.5 and APX4 2.5. Here are the detailed base image [release notes](https://docs.auterion.com/release-notes/flight-control/apx4-2.5/apx4-2.5.0)
* **Known Issues**
  * Switching from photo to video mode will work, however AMC will display an incorrect warning that it failed.

</details>

<details>

<summary>Herelink v1.0.1</summary>

* **Summary**: Herelink bugfix release
* **Release Date**: September 2021
* **Versions in this package**:
  * Herelink OEM build number: FFSRU01210809
* **Notes**:
  * Bugfix: This version fixes an issue with the wifi hotspot intermittently stopping to work.

</details>

<details>

<summary>Astro v1.0.21</summary>

* **Summary**: Astro hotfix release
* **Release Date**: August 2021
* **Versions in this package**:
  * Astro Skynode: v1.0.21
* **Notes**:
  * Bugfix: Slew rate limits are enabled to prevent an edge case where aggressive motor commands can cause motor controller to destabilize.

</details>

<details>

<summary>Astro v1.0.18</summary>

* **Summary**: Initial Astro release
* **Release Date**: July 2021
* **Versions in this package**:
  * Astro Skynode: v1.0.18

</details>

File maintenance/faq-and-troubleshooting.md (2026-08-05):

---
icon: circle-question
---

# FAQ & Troubleshooting

## Known Issues and Solutions

<table data-search="false"><thead><tr><th>Issue</th><th>Solution</th></tr></thead><tbody><tr><td>Battery cells out of balance</td><td>Leave on the charger (under supervision) for about 8 hours</td></tr><tr><td>Cannot control gimbal</td><td>Update Astro and controller. <br><a data-mention href="software-release-notes/">software-release-notes</a></td></tr><tr><td>Astro drifts up/down while hovering</td><td><a href="https://freefly.gitbook.io/astro-public/astro/maintenance-manual/calibration-and-tuning#sensor-calibration">Calibrate accelerometer</a></td></tr><tr><td>Cannot record video using the Sony a7R-IV, or "unable to write to card, check card speed"</td><td>Install a faster SD card into the camera</td></tr><tr><td>Can't connect laptop version of AMC to Astro</td><td>Change the <a href="https://freefly.gitbook.io/astro-public/astro/ecosystem/components/pilot-handsets#hotspot">UDP settings</a></td></tr><tr><td>Gimbal is limp with camera on</td><td><p>Ensure the Astro firmware and your gimbal firmware are both up to date.</p><p> <a data-mention href="software-release-notes/software.md">software.md</a></p></td></tr></tbody></table>

## FAQ

| Question | Answer |
| --- | --- |
| Is there a compatible LiDAR sensor? | <p>Yes! Freefly offers the <a href="https://app.gitbook.com/s/WXREyAKYAeQJ4gfg2SPg/payloads/flux-lidar">Flux Lidar payload </a>for super fast in-field processing. </p><p><a href="https://app.gitbook.com/s/WXREyAKYAeQJ4gfg2SPg/payloads/third-party-payloads/hovermap-st-x-and-st-lidar">Hovermap ST-X</a> offers autonomous flight in GPS-denied environments.</p><p><a href="https://freeflysystems.com/payloads">See all compatible LiDAR payloads</a>.</p> |
| Is there a thermal sensor for Astro? | <p>Yes, Freefly offers a <a href="https://app.gitbook.com/s/WXREyAKYAeQJ4gfg2SPg/payloads/lr1-payload/expansion-modules/lr1-thermal-module">thermal module upgrade</a> for the Sony LR1 mapping payload.<br><br><a href="https://freeflysystems.com/payloads">See all compatible thermal payloads.</a></p> |
| Where can I find my Astro's serial number?  | <p>The serial number can be found on the belly of the aircraft, near the vibration isolator.<br></p> |
| | |

## Advanced Troubleshooting

For in-depth problem-solving, you can check our [Troubleshooting Tree](https://docs.google.com/spreadsheets/d/1DXkk0BmRx9qLbjpBt2KgKYFOQhEGUTcyyQB6rOmb4ac/edit#gid=528435697) or [Astro Support page](https://freeflysystems.com/support/astro-support) for solutions to specific questions or error codes.&#x20;

If you need more help or can't find what you're looking for, please [contact us](https://freeflysystems.com/contact)!

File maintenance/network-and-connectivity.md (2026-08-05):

---
icon: circle-wifi
---

# Network and Connectivity

## WiFi

This section describes the connection process for Astro's built-in wifi chip. This functionality is useful while the aircraft is on the ground, for admin and setup tasks.&#x20;

{% hint style="warning" %}
By default, Blue/NDAA Astros have WiFi and LTE disabled for DIU Blue compliance.&#x20;

For more information, see [diu-blue-suas.md](../other-user-manuals/compliance/diu-blue-suas.md "mention")
{% endhint %}

### Connect the Astro aircraft to a WiFi network

{% tabs %}
{% tab title="Video" %}
{% embed url="https://www.loom.com/share/b81f0678863947c192e09fe474aee709" %}
{% endtab %}

{% tab title="Text" %}
1. Open AMC GCU or PC. If using a PC, connect to Astro with a USB-C cable.
2. Tap on the vehicle status button at the top of the AMC screen (it will be either red, yellow, or green depending on the vehicle's status).
3. Select Connectivity.&#x20;
4. Enable Wifi and disable Hotspot Mode.&#x20;
5. Enter the Network SSID and Password for your wifi access point and select Connect.&#x20;
{% endtab %}
{% endtabs %}

### Connect to the Astro hotspot via WiFi

Astro has the ability to broadcast a WiFi hotspot so that you can connect to it wirelessly using another device, such as your phone.&#x20;

1. Open AMC. If using AMC on a desktop computer, connect to Astro with a USB-C cable.
2. Power on Astro with one battery (this prevents accidental arming for safety)
3. Tap the icon in the top-left of AMC. Navigate to Vehicle Overview > Connectivity > WiFi
4. Turn on "Hotspot Mode", which allows Astro to broadcast a WiFi network that other devices can connect to.

## LTE

If your Astro has a data SIM card installed, it can connect to an LTE network. This is used for some cloud features available in Auterion Suite, such as automatic flight upload, live video streaming, and more.

{% hint style="warning" %}
By default, Blue/NDAA Astros have WiFi and LTE disabled for DIU Blue compliance.&#x20;

For more information, see [diu-blue-suas.md](../other-user-manuals/compliance/diu-blue-suas.md "mention")
{% endhint %}

### Configure and Enable / Disable

1. [Install a SIM card](standard-maintenance-procedures/replacing-components/installing-a-sim-card.md) into Astro. Make sure to write down the SIM card number found on the card if you don't have it recorded elsewhere.&#x20;
2. Open AMC
3. Navigate to Vehicle Overview > Connectivity > LTE and enable it.
4. If you need to access the IMEI number for the vehicle to enable the SIM cards, connect to the Astro with a laptop and USB cable
   1. Power on Astro with one battery only.
   2. Connect the laptop and the Astro by plugging in a USB-C cable to the IO panel on the underside of the aircraft.
   3. Using a web browser, navigate to `10.41.1.1` to connect to your Astro's web UI.
   4.  On the bottom of the page, expand the "details" bar and scroll until you find the listed IMEI information<br>

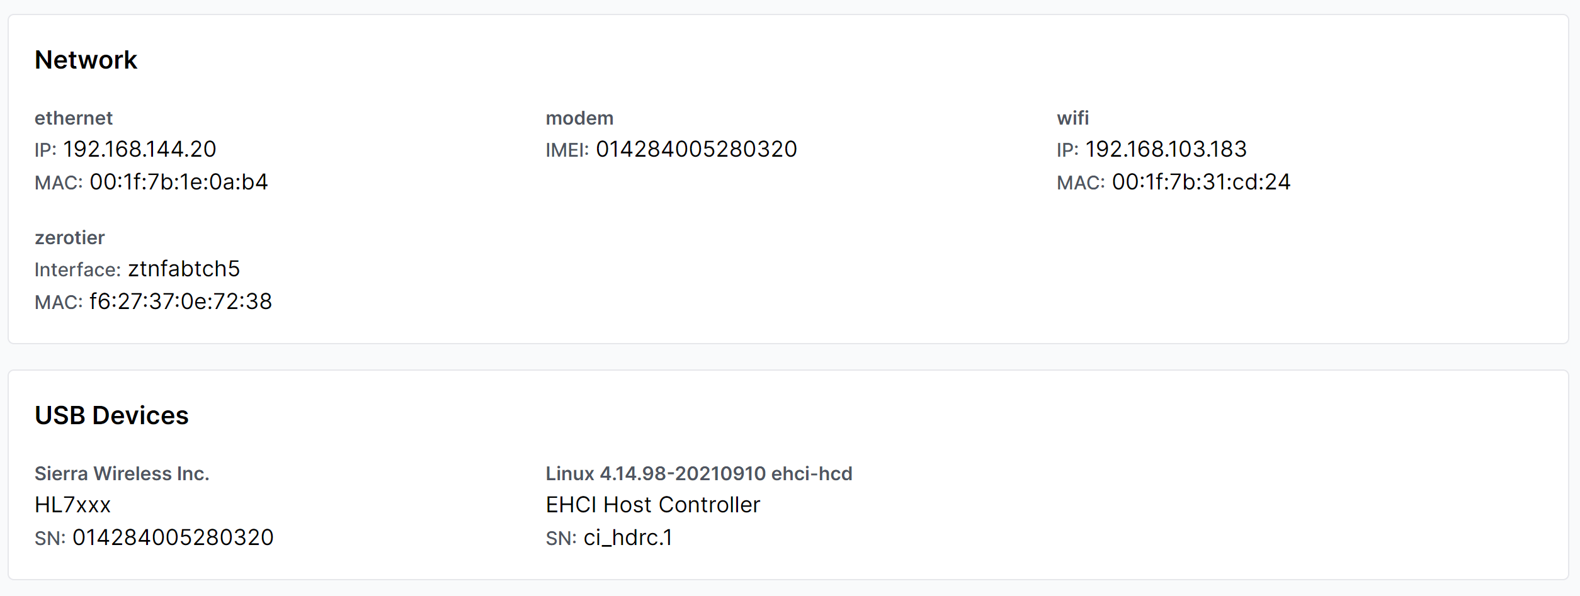
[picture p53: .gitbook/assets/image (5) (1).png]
       <figure><figcaption></figcaption></figure>

### Hardware Disable

You can assure that LTE is not being used by[ removing the SIM ](https://freefly.gitbook.io/astro-public/astro/maintenance-manual/replacing-components/installing-a-sim-card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)card from Astro.&#x20;

### Frequencies and Compatibility

| Region | 4G LTE Bands | Radio Spec Sheet |
| --- | --- | --- |
| North America (United States, Canada) | B2, B4, B5, B13, B17 | [Sierra Wireless](https://source.sierrawireless.com/devices/hl-series/hl7519-48-88/) |
| EMEA/Australia | Cat-4: B1, B3, B7, B8, B20, B28 | [Sierra Wireless](https://www.sierrawireless.com/iot-modules/smart-modules/rc7620/)  |

{% hint style="warning" %}
Currently, Astro is only available with an LTE radio suitable for North American markets (USA & Canada). Additional LTE compatibility will be available in the future.
{% endhint %}

### Changing SIM / Service Provider

When switching SIM cards, try leaving the APN field blank. It should be automatically detected. If not, here are a few suggestions.

| Carrier  | APN |
| --- | --- |
| T-mobile | iot.tmowholesale, fast.t-mobile.com |
| Orange | orange.m2m.spec |

{% hint style="info" %}
T-Mobile and Orange are tested and known working providers.&#x20;
{% endhint %}

In most cases, check the "Allow Roaming" box.

After changing the SIM, reboot both the aircraft and AMC.

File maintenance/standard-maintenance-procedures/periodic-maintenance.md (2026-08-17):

---
description: Everything you need to know to maintain a safe and functional aircraft
---

# Periodic Maintenance

{% hint style="danger" %}
Before performing any maintenance, ensure that Astro is not connected to any power source, battery or otherwise. Leaving Astro powered while performing any work on it can result in a potentially dangerous situation.
{% endhint %}

## General Notes

### Cleaning

Keep your aircraft free of dust and debris after each use. This prevents moving parts from becoming damaged, worn, or jammed. It also prevents contamination from concealing structural damage during visual preflight inspections.

Clean Astro's exterior with a non-abrasive soft cloth, microfiber towel or similar with a plastic-safe soap or detergent. Graduate the solvent potency when removing contamination, as shown below:

1. Water
2. Soap and water
3. General cleaner (like Simple Green)
4. Isopropyl Alcohol

Avoid anything that has bleach in it, or aggressive solvents like Acetone. If operating in a salt environment, wipe down Astro after use with a clean rag wet with tap water.

## Preventative Maintenance Schedule

Always follow the preflight checklist items to ensure that each flight is safe and achieves the mission goals.

Astro is rated for 1,500 flight hours. Items not listed in a preventative maintenance schedule have a service life equal to the aircraft’s lifetime. This includes all aircraft electronics and motors.

At any point if you are concerned about something on the aircraft you can contact Freefly Support or purchase a Preventative Maintenance Checkup.

{% hint style="warning" %}
Note: it is key to keep both your aircraft and controller firmware up to date. See: [Software Release Notes](../software-release-notes/)
{% endhint %}

### PM1: Every Flight

* Perform a full visual inspection of the drone, controller, batteries, and payloads before each flight.
* Look for any missing screws or hardware, any new damage or cracks, or anything that looks out of the ordinary or has changed.
* Check that motors spin freely and with no grinding/interference
* Developing this mental model of your drone is key to catching issues before they become a possible in-flight emergency.

### PM2: Every 15 Flight Hours

_In addition to phase PM1:_

**Perform a detailed visual inspection of the aircraft:**

* Propeller blades and fasteners
  * Motor mounting fasteners are present and not loose
  * Propeller blades are flight ready. Reject if chips, cracks, or deep scratches are visible. Replace as necessary with spare parts.
* Vibration Isolators:
  * Visually check for any cracks, gel leaks, visible stretching. Replace as necessary with spare parts
* Propeller blade washers (between blade and hub):
  * Verify that each washer is present and not severely deformed. Replace it as needed with a spare part.
* Inspect Landing Gear
  * Look for: Loose hinges, Hinge pin migration, no longer latching, any visible cracks or damage

**Clean aircraft**

* Wipe down any dust/debris from chassis
* Clean any contamination from battery connectors
* Ensure no debris in or around the boom motors
* Clean off any debris on propellers

**Check Propeller Tension**

* Verify that propeller tension is within the acceptable range. The propeller must not be clamped too tightly or too loosely.

**Verify Boom Latch Tightness**

* Verify each boom fully latches
* The safety hinge has a solid over-center force
* The hinge latch fully seats behind the latching post
* If the hinge does not have enough tension, use a driver to adjust the hinge set screw to increase the latch tension

### PM3: Every 3 Months: SL8 Battery Maintenance

* Ensure that any battery storage is conforming to the [Maintenance Guidelines](https://docs.freeflysystems.com/ecosystem/power/superlight-batteries/maintenance) in the battery user manual
* Visually inspect each battery:
  * Verify housings are intact and have no structural damage
  * Verify the battery connector has no major damage
    * Note: It is possible for the connector to get small minor chips from high force insertion on the Astro. This is OK as long as no connector metal is exposed from the damage.
    * If you have any questions, send a photo of the connector to Freefly Support
* Verify that the battery does not have any errors displayed on the OLED screen

### PM4: Every 250 Flight Hours

_In addition to phases PM1 and PM2:_

**Inspect all fastener locations to verify fasteners are present, not damaged, and are not loose.**

Check the tightness of the following fasteners to verify no loose fasteners or use a torque stripe/seal to ensure bolts have not moved.

To check fasteners, apply a slight tightening torque (Clockwise direction) to each fastener on the chassis using the supplied hex drivers. The fasteners should not slip. Do not try to tighten the fastener, only check if it is loose

* If a fastener does slip, tighten it using the methods described in the "Replacing Components - Fastener Specifications" section. Do not apply additional thread locking compound unless the fastener has repeatedly come loose.

#### Items that need tightness verified (ensure they have not worked loose):

* Motor mount bolts (attaches motor mount to boom)
* Propeller Mount bolts (attaches props to motor)
* Prop Tension (see [prop tension](replacing-components/replacing-propellers.md#prop-tension))
* Top and bottom chassis bolts
* Payload Isolation Mount
* Compass mounting bolts
* GPS antenna tightness
* Landing Gear bolts
* Any payload fasteners

### PM5: Every 750 Flight Hours

* Freefly recommends to perform this maintenance every year even if the aircraft has not hit 750 flight hours, especially if the aircraft has missed other PM intervals or if the drone operates in harsh or abusive conditions
* Send Astro in for a Freefly Service Inspection and Overhaul
  * Freefly drone service team will perform a full visual inspection and functional test of your aircraft with specific emphasis on:
    * Wear/fatigue items
    * Updated/improved/revised components
    * Confirm performance thresholds
      * Motors
      * Sensors
      * Any payload stabilization metrics
    * The service will include:
      * Historical flight log review for any errors or trends that need to be addressed (shared via Auterion Suite)
      * Service bulletin and firmware updates.
      * Full airworthiness inspection
      * Full cleaning and fastener replacement (as needed)
      * System level test and re-qualification

## What to do if an Inspection Fails?

The first step is to determine whether you can fix the problem. Users can typically resolve the following issues:

* Dirty or contaminated hardware
* Loose fasteners (Ensure you have the correct type of Loctite Threadlocker)
* Missing fasteners (If you have the correct replacement parts)
* Any replacement parts that you bought from the store or have specific directions from Freefly Customer Support

If you have a failure and cannot fix using our general guidelines or the spare parts provided in the kit or on the store, please reach out to support@freeflysystems.com or [submit a direct ticket](https://freeflysystems.com/contact) for any questions, specific replacement needs or issues! We are here to help you get safely and quickly back into the air!

If you need to purchase spare or replacement parts, please go to [store.freeflysystems.com](http://store.freeflysystems.com) to purchase our standard parts.

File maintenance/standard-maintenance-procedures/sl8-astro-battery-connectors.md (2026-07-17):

# SL8/Astro Battery Connectors

**We recommend all Astro pilots routinely check the aircraft and SL8 battery connectors for signs of damage, debris, or excessive wear.**

## Inspect Connectors&#x20;

* Inspect the battery connectors on Astro for melted plastic and / or solder at the base of the power pins. **Do not fly Astro if a connector is damaged** and contact Freefly Support for further guidance . Note some wear and marking is normal on Astro side connectors &#x20;
* Inspect all SL8 battery connectors for melted plastic, debris, or dirt. **Do not fly any SL8 battery if the connector is damaged** and contact Freefly Support for further guidance.&#x20;
* Debris and dirt can be gently removed with compressed air from the SL8 connector
* Astro aircraft side connectors can be cleaned with compressesd air or with a toothbrush and 99% Isoproply Alcohol&#x20;

{% hint style="danger" %}
Never remove debris from the battery with tweezers. If debris cannot be removed from the battery with compressed air, the battery may need to be returned to Freefly or disposed of.&#x20;
{% endhint %}

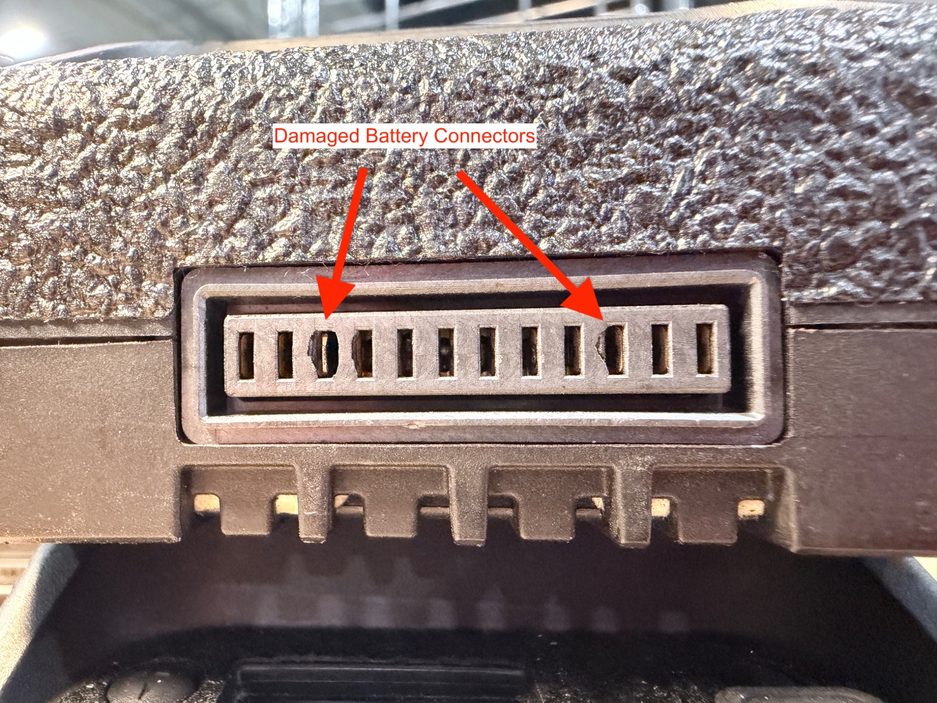
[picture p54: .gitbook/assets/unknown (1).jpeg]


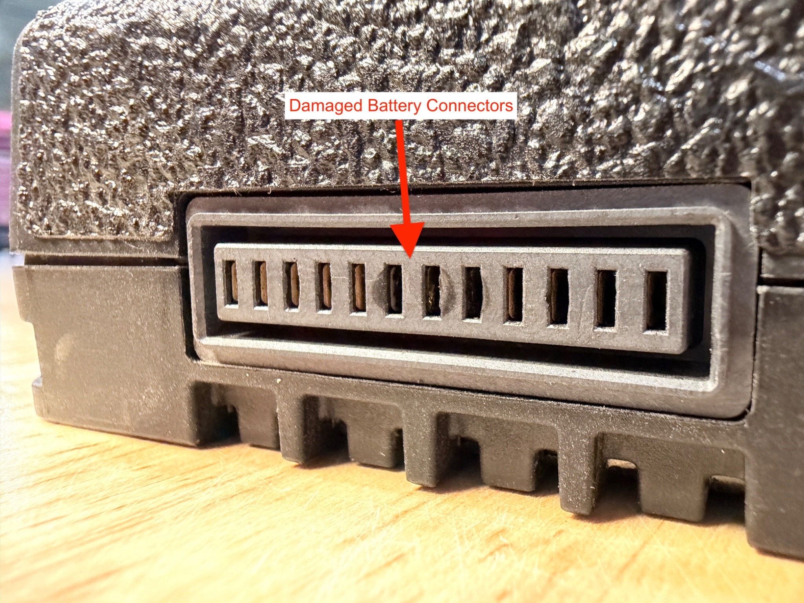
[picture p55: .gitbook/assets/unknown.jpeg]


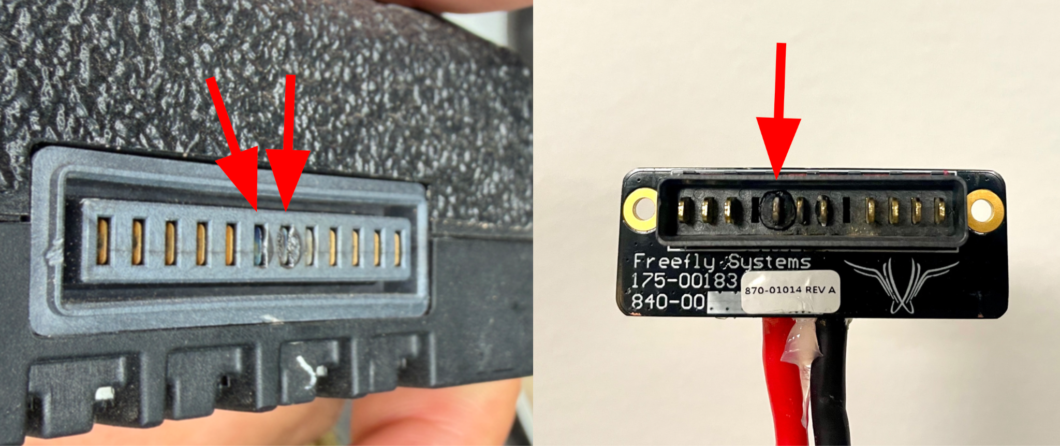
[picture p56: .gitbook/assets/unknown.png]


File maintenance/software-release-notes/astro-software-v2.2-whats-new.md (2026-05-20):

# Astro Software v2.2 - What's New

{% embed url="https://www.youtube.com/watch?v=SnKNH_42jXQ" %}

***

### New: Doodle Radio Channel Scan

The Doodle channel scan has been rewritten for more reliable channel scan results and selection.

* This includes new channel scoring algorithm during scan, as well as UI improvements.
* Note: Typical Wifi routes, Herelink, and most non-mesh interference sources are detected correctly. However Doodle Labs mesh radios **on the same channel** are not detected by this metric.
* Working with Doodle radios can be challenging in in high interference environments. Please refer to [Doodle Pro Tips](https://docs.freeflysystems.com/ecosystem/controller/pilot-pro/operating-handbook/radio-modules/doodle-labs-radio-module/doodle-pro-tips) article, as well the new [Channel Scan](https://docs.freeflysystems.com/ecosystem/controller/pilot-pro/operating-handbook/radio-modules/doodle-labs-radio-module/doodle-channel-selection) feature article for more guidance.

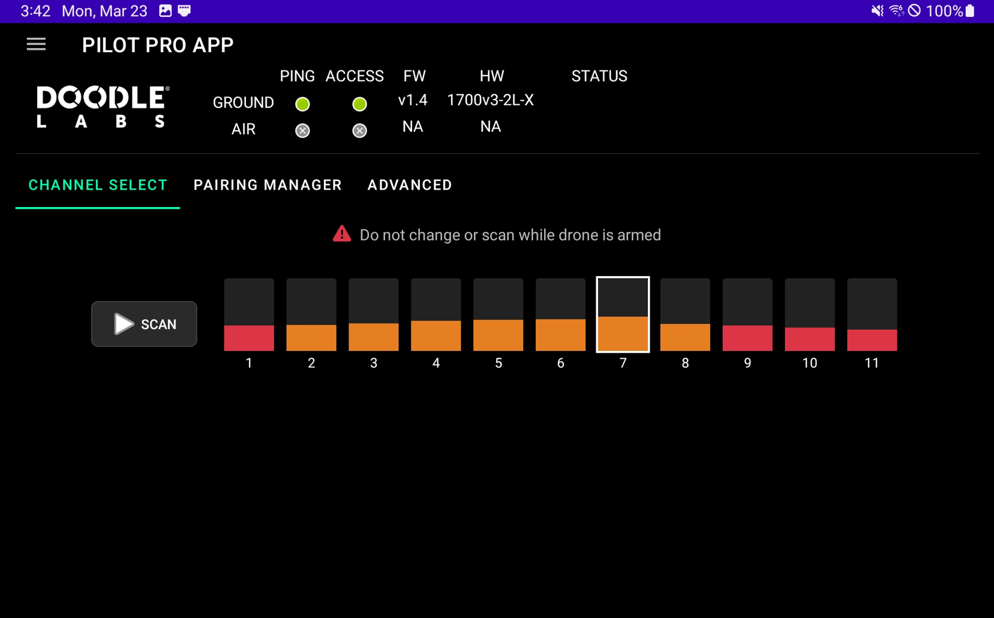
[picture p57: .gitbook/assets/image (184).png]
<figure><figcaption></figcaption></figure>

***

### New: RTK and NTRIP from Pilot Pro

* You can now run Freefly RTK or NTRIP corrections directly from the Pilot Pro App on MAVLink-over-ethernet vehicles (Astro and Alta X Gen2), with no separate Astro side app required.
* Supports VRS and fixed mountpoints.&#x20;

{% hint style="info" %}
Unlike the Astro-side NTRIP app option, Pilot Pro does not auto-start NTRIP on boot. This is intentional, since corrections consume radio bandwidth and should be an explicit per-flight choice.
{% endhint %}

<a href="https://docs.freeflysystems.com/ecosystem/controller/pilot-pro/operating-handbook/ecosystem/rtk" class="button primary">Learn More</a>

***

### New: LR1 and A7R Payload Features

* **Fixed Focus mode:** Alongside Infinity and Auto, you can now select **Fixed** to lock the camera at its current focus distance. Common workflow: tap-to-focus on a near subject, then switch to Fixed to keep that focus for subsequent shots. This is helpful for both inspection use cases, as well as mapping.
  * Pro-tip: To best use Fixed Focus mode, enable it in the camera settings > 'Focus Mode' dropdown. You can then temporarily enable the 'Tap to Focus' selector to adjust focus - be sure to disable Tap to Focus to re-enable Fixed Focus mode.
* **APS-C crop support in video mode:** Exposes the APS-C Size Capture setting directly in AMC's payload controls.
* **Additional video recording formats:** XAVC S-I 4K and additional frame-rate and record-setting combinations are now available.
* **RAW and RAW+JPEG:** New File Format options in the LR1 Photo Mode. RAW images save to the camera SD card only (file sizes would otherwise saturate the USB pipeline). Digital zoom is disabled in RAW modes.
* **Fix: Blurry Infinity Focus on Sigma 24mm lens v.03:** The payload driver now reads the lens firmware version and applies the correct focus offset for v.01, v.02, and v.03 lenses. Detection is automatic on LR1 and via EXIF on A7R.

{% hint style="info" %}
To use APS-C mode, [update your LR1 camera to firmware v3.0 or later.](https://docs.freeflysystems.com/ecosystem/payloads/payload-maintenance/payload-camera-firmware-update) LR1 cameras on firmware v1.0.0 do not reliably accept the APS-C command. Early-batch LR1s (unit shipped before October 2024) are most likely to be on v1.0.0.
{% endhint %}

***

### New: Boson Isotherm and Contrast Setting Improvements

* **Wildfire Contrast Preset:** A new "Wildfire" option in the Contrast Preset dropdown pre-configures the Advanced Contrast Settings and Isotherm views for wildfire detection, built together with the U.S. Forest Service.
* **Simplified Isotherm Views:** Two new modes, **Temp Above** and **Temp Below**, each enable a single isotherm band so it's easy to highlight just the hottest (or coldest) objects in frame.
* **Advanced Contrast Settings moved:** Modifying the Advanced Contrast Settings is now in its own dropdown. Changing the Contrast Preset resets all Advanced Contrast Settings to the preset's values.
* **Radiometric TIFF captures are much faster**

***

### New: Gremsy VIO is now plug-and-play

* Swapping between an LR1 and a Gremsy VIO gimbal used to require manually setting `MNT_RATE_YAW = 0` so the zoom rocker wouldn't also command gimbal yaw. The default is now 0 on Astro, so VIO payloads work out of the box.
* Swapping between LR1 and VIO no longer requires any parameter changes.

{% hint style="info" %}
The VIO must be [configured correctly](https://app.gitbook.com/s/WXREyAKYAeQJ4gfg2SPg/payloads/third-party-payloads/gremsy-vio), or [purchased from Freefly.](https://store.freeflysystems.com/products/gremsy-vio-f1-for-astro-alta-x-gen2)&#x20;
{% endhint %}

{% hint style="info" %}
To use VIO geotagging, the aircraft must be [switched to MAVLink mode](https://docs.freeflysystems.com/ecosystem/payloads/third-party-payloads/gremsy-vio#astro-configuration), which removes the blue configuration of the aircraft.
{% endhint %}

***

### More Quality Of Life Improvements

* Payload: Addressed an issue that was causing gimbal horizon drift.
* Payload: Gimbal now auto positions itself after powered on, even if its mounted inverted.&#x20;
* Pilot Pro: Status page can now be customized by Pilot Pro integrators
* Drone: Strong Magnetic Interference Warning text has been updated for clarity so the pilots can take appropriate action instead of treating it as a blocker. If the status indicator in AMC is RED, then the aircraft is blocked from arming. If the status indicator is yellow/orange, then arming is possible but warnings are still present for increased pilot awareness.
* Drone: Improved GPS reliability. Mitigates the known issue in [Astro SB012](https://freeflysystems.com/knowledge-base/astro-sb012-astro-software-v2-1-13-addresses-service-bulletins-sb010-and-sb011).
* Drone: Mission uploads are now logged into the ulog for customer support and debugging.
* Drone: Fix various edge cases to improve PX4 flight controller reliability.

***

### How To Update Software?

Astro ->  [#latest-versions](./#latest-versions "mention")&#x20;

Alta X Gen2 -> [Software Updates #Current Firmware Version](https://app.gitbook.com/s/mvvtTxCd0o4luBB04PQp/maintenance/software-updates#current-firmware-version "mention")

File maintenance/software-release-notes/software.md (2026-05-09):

# Updating Firmware

## Updating Astro Firmware

{% hint style="info" %}
You can determine if Astro needs an update by following steps 2-4 below. The current firmware number available will be on the [Software Release Notes](./#current-firmware-versions) page.
{% endhint %}

1. [**Download**](https://freeflysystems.com/support/astro-support) the firmware file from the [**Astro Support page**](https://freeflysystems.com/support/astro-support) or [the Suite](https://suite.auterion.com/downloads/firmware).
2. Connect Astro to your computer with a USB cable.
3. Power on aircraft **with one battery** and wait about 15 seconds for aircraft to fully boot.
4. Using a browser such as Chrome or Safari, open the aircraft's info/update page at [http://10.41.1.1](http://10.41.1.1) (internet connection is not needed).
5. In the Update AuterionOS box, click Browse, and select the firmware file downloaded above.
6. Click Update. (Should take about 10 minutes.)
7. After the update completion message, verify that the webpage shows a "Release name" that matches the downloaded file and that all the motor LEDs are on.

{% hint style="warning" %}
**If your Astro firmware update fails:**

1. Update the Pilot Pro App to v2.7 or later.
2. Connect Pilot Pro to your Astro.
3. Tap the **Fix Me** button in Pilot Pro, which will apply the _FW Updater Fix_. This is found in:\
   &#x20;`App Menu > Vehicle Status Page`&#x20;
4. If you have a Blue/NDAA Astro, you will need to disable Admin Protection on the 10.41.1.1/settings page before the _FW Updater Fix_ can apply. Admin Protection can be re-enabled after the Astro firmware update is successful
5. Retry the Astro firmware update once the _FW Updater Fix_ has been applied.
{% endhint %}

{% hint style="warning" %}
After updating the aircraft, make sure that all apps in the Freefly Updater on your controller are [up-to-date](https://freefly.gitbook.io/astro-public/maintenance/standard-maintenance-procedures/herelink-controller-maintenance/updating-herelink-software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).&#x20;

If Freefly Updater is not installed, follow these [instructions](https://freefly.gitbook.io/astro-public/maintenance/standard-maintenance-procedures/herelink-controller-maintenance/switching-to-freefly-updater).
{% endhint %}

### Checking Astro Firmware Version

{% tabs %}
{% tab title="Video" %}
{% embed url="https://www.loom.com/share/f0697b699e944b7da68ce24e7cbfa081" %}
{% endtab %}

{% tab title="Text" %}
* Connect Astro to your computer with a USB cable.
* Power on aircraft **with one battery** and wait about 15 seconds for aircraft to fully boot.
* Using a browser such as Chrome or Safari, open the aircraft's info/update page at [http://10.41.1.1](http://10.41.1.1) (internet connection is not needed).
{% endtab %}
{% endtabs %}

***

## Updating Herelink Firmware

As of Astro Version 1.4.6, Herelink is maintained through the Freefly Updater. Instructions on how to install the Freefly Updater can be found [here](https://freefly.gitbook.io/astro-public/maintenance/standard-maintenance-procedures/herelink-controller-maintenance/switching-to-freefly-updater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).&#x20;

Once the Freefly Updater has been installed, it can be used to [update AMC and other apps](https://freefly.gitbook.io/astro-public/maintenance/standard-maintenance-procedures/herelink-controller-maintenance/updating-herelink-software).&#x20;

***

## How to Reset to Default Astro Parameters

{% tabs %}
{% tab title="Video" %}
{% embed url="https://www.loom.com/share/fed073ac16ba4bac937565dbee04dbb2?sid=0e7d0dab-7543-48fc-95fb-95e4ef270bc5" %}
{% endtab %}

{% tab title="Text" %}
* Open AMC and [activate Advanced mode](https://freefly.gitbook.io/astro-public/astro/pilots-operating-handbook/software/auterion-mission-control/amc-vehicle-setup/advanced-vehicle-setup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)
* Connect AMC to Astro
* Select: Vehicle setup > Parameters > Tools > Reset to vehicle's configuration defaults.
* Reboot Vehicle
* Calibrate sensors as required
{% endtab %}
{% endtabs %}

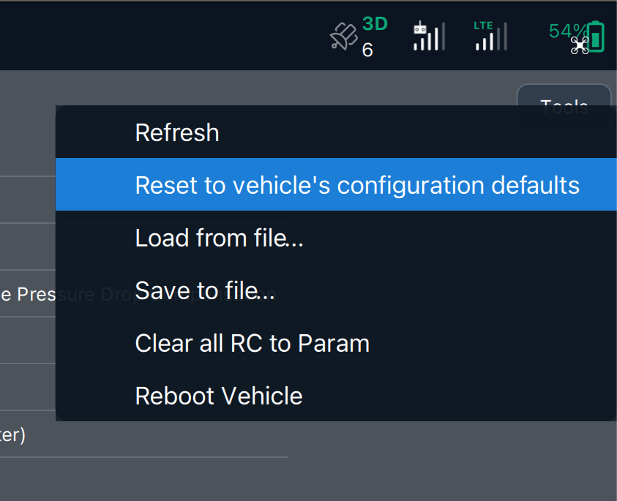
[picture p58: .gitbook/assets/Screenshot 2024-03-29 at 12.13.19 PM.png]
<figure><figcaption></figcaption></figure>

##

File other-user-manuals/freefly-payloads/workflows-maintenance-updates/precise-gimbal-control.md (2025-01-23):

---
description: How to fine-tune the gimbal pointing controls
---

# Precise Gimbal Control

## Tilt Control&#x20;

The payload's tilt rate scales with zoom. This means that as the digital zoom level is increased, the gimbal's tilt rate will decrease to provide pointing control.

{% hint style="info" %}
The overall gimbal tilt speed (slow/med/fast) can be adjusted under the camera settings.&#x20;
{% endhint %}

## Yaw/Pan Control

By default, the aircraft's yaw control is unaffected by the camera's zoom level; however, zoom rate scaling can also be applied to yaw/pan through Slow Speed Mode.&#x20;

For even more control, the global yaw rate of Astro can also be adjusted if desired. The default global yaw rate of Astro is 75 degrees/second.&#x20;

* The max yaw rate can be adjusted by going to Advanced Mode (tap the AMC logo in the upper left-hand corner seven times). Then click on the Auterion logo again and click through Vehicle Setup -> Parameter -> MPC\_MAN\_Y\_MAX. The units are in degrees/second.&#x20;

{% hint style="danger" %}
Be careful when changing parameters, and double-check what you are doing. Changing the wrong parameter can cause unexpected behavior or even a crash!
{% endhint %}

### Slow Speed Mode&#x20;

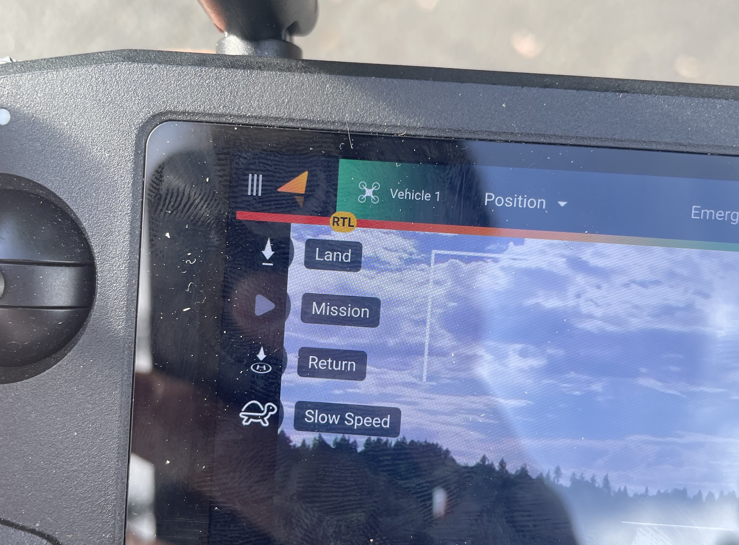
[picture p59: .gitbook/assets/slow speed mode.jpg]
<figure><figcaption></figcaption></figure>

Slow Speed mode is a togglable flight mode that affects the sensitivity of the aircraft's yaw when the camera is zoomed in.&#x20;

* Slow Speed mode can be toggled on and off when Astro is in Position mode. It's active when the icon is lit, and you view the video stream.
  * Slow Speed mode will automatically deactivate when viewing the IR stream&#x20;
  * Slow Speed mode is turned off by default

{% hint style="info" %}
Only the aircraft's yaw speed is affected, not the maximum translational/vertical speed of the aircraft.
{% endhint %}

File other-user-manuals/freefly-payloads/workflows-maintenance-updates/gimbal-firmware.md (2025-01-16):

# Gimbal Firmware

## Latest gimbal firmware

| | LR1 Payload | OGI Payload | Wiris Pro Payload | A7R4 Payload |
| --- | --- | --- | --- | --- |
| **Astro Firmware 1.6 or later** | v2.1.0 | v2.1.0 | v1.7.2 | v1.7.2 |
| **Astro Firmware 1.5 or older** | Not supported | Not supported | v1.6.2 | v1.6.2 |

{% hint style="info" %}
Make sure to update Astro and AMC to the latest FW too!
{% endhint %}

## How to check gimbal firmware

<figure><figcaption><p>Note: Payload must be connected to Astro to check version number</p></figcaption></figure>

Gimbal firmware versions are also included in gimbal log files

{% content-ref url="gimbal-logs.md" %}
[gimbal-logs.md](gimbal-logs.md)
{% endcontent-ref %}

## Gimbal firmware release notes

### v2.1.0

* Initial Release for OGI Payload
* Updated 75mm tuning for LR1 on Astro with large motors

{% file src="../../../.gitbook/assets/minigimbal_lr1_v2.1.0 (1).zip" %}

{% file src="../../../.gitbook/assets/minigimbal_ogi_v2.1.0 (1).zip" %}

### v2.0.2

* Initial release for LR1 Payload

{% file src="../../../.gitbook/assets/minigimbal_lr1_v2.0.2.zip" %}

### v1.7.2 

{% file src="../../../.gitbook/assets/minigimbal_a7r4_v1.7.2.zip" %}

{% file src="../../../.gitbook/assets/minigimbal_wiris_pro_v1.7.2.zip" %}

* Change: baud rate to enable reliable parameter forwarding
* Bugfix: now handles mavlink forwarding turned on

This is a required firmware update for Astro's running firmware 1.6 or later. This gimbal firmware will only work on Astro FW 1.6 and later

### v1.6.2 

{% file src="../../../.gitbook/assets/minigimbal_a7r4_v1.6.2.zip" %}

{% file src="../../../.gitbook/assets/minigimbal_wiris_pro_v1.6.2.zip" %}

* **Bugfix: Fixed the SD card corruption issue, preventing the gimbal from powering on**
* New: Added tilt limits to mongoose of -90 and +30 degrees tilt
* Improvements:
  * Improved heading control
  * Calibration and process updates to improve attitude performance
  * Added GPS date time as supplied by Astro to log

### v1.0.1 

* Initial Release

## Updating Gimbal Software

1. Download the firmware package.
   * Extract the .zip folder contents.
   * Open the extracted folder- the top level folder that you will need to copy onto the gimbal will be called "freefly". Do not copy the folder that states the firmware version.\

2. To upgrade Gimbal firmware, connect the gimbal to a laptop using a USB-C cable.&#x20;
   * The USB-C connector is located on the Smart Dovetail of the gimbal
   * Ensure the gimbal is not powered by the aircraft
   * The gimbal will show up on the computer as an external drive called "FREEFLY"

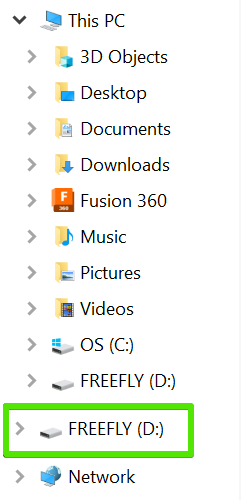
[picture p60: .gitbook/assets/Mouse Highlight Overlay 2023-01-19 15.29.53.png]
<figure><figcaption></figcaption></figure>

3. Open that drive and you will see a folder named "freefly". This is the current firmware file that you need to replace.&#x20;
   * Delete this folder and replace it with the new firmware folder "freefly' that you downloaded in Step 1

<figure><figcaption></figcaption></figure>

4. Remove the USB-C cable from the gimbal and connect the gimbal to an Astro using the Smart Dovetail to power on the gimbal.&#x20;
5. Insert 1 SL8 Battery into the aircraft and fully latch the battery, but **do not** power on the aircraft at this time.
6. Use a paperclip or small screwdriver to hold down the Firmware Load button on the gimbal- this button must be pressed and held for 10 seconds while powering on the aircraft.
   * This small button is recessed into the gimbal housing and is located next to the USB-C connector on the Smart Dovetail.
7. Power on the aircraft by double clicking the button on the SL8 battery.&#x20;
   * Ensure that the Firmware Load button is held down during this time for 10 seconds while the new firmware is loaded onto the gimbal.
8. When firmware is successfully updated, the gimbal should stabilize correctly and video feed will show on the controller.

## Camera Software

We have tested LR1 cameras on 1.00 FW. We do not recommend any updates to the camera as it may cause compatibility issues with Astro and AMC.&#x20;

## Gimbal Logs

With Astro off or with the gimbal removed from the aircraft, connect a USB-C cable between a computer and the USB-C port on the payload side of the dovetail. A drive will mount on your computer. The logs are located under "freefly\movi\logs".

## Gimbal Baud Rate

If you're experiencing a limp gimbal upon powering on or during flight, this could be caused by a baud rate mismatch between your gimbal and Astro system. To resolve the issue, ensure that both your gimbal and Astro are running compatible firmware versions.

**Firmware Changes:** Starting with Astro firmware version 1.6, the baud rate for communication between the Astro system and the gimbal was updated. In Astro firmware 1.5 and earlier, the baud rate was set to **921600 8N1**. However, with the release of firmware 1.6, the baud rate was increased to **230400 8N1**. This should update automatically by applying firmware 1.6 or later

**How to Check Gimbal Baud Rate:** To verify your gimbal's baud rate, [access the advanced parameters](https://freefly.gitbook.io/astro-public/pilots-operating-handbook/essential-software/auterion-mission-control/amc-vehicle-setup/parameters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) in your system and locate the **SER\_EXT2\_BAUD** parameter. This will indicate the current baud rate setting on your gimbal.

By ensuring that both your gimbal and Astro firmware are using compatible baud rates, you can prevent any communication issues and maintain proper gimbal functionality.

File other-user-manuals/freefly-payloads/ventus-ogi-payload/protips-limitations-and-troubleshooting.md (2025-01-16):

# Protips, Limitations, and Troubleshooting

## First things first&#x20;

{% hint style="success" %}
The OGI Payload is supported in Astro firmware version 1.9.1 or later. Update your Astro!
{% endhint %}

{% hint style="info" %}
Make sure to update the Pilot Pro controller to the latest version, too!
{% endhint %}

{% hint style="info" %}
When powered on, the Ventus OGI may take about 10 minutes to cool down and calibrate. If you power off for only a short time, the calibration time is reduced. You do not have to wait for the cooldown to be completed before taking the flight.
{% endhint %}

{% embed url="https://freefly.gitbook.io/astro-public/astro/maintenance-manual/software" %}

## #Protips

{% hint style="success" %}
Slow speed mode makes the gimbal easier to control when zooming in.
{% endhint %}

&#x20;Learn about it under the [Precise Gimbal Control](https://freefly.gitbook.io/astro-public/astro/payloads/wiris-pro-payload/operating-handbook/precise-gimbal-control) section

{% hint style="warning" %}
Be careful not to become disoriented when flying with the camera zoomed in. We recommend resetting the camera zoom to 1x before flying to a new inspection location.
{% endhint %}

## Limitations

#### Gimbal

{% hint style="warning" %}
Do not hot-swap or plug in the gimbal when the aircraft is powered on. This can damage the aircraft or gimbal.
{% endhint %}

{% hint style="warning" %}
Make sure you are using the correct vibration isolator
{% endhint %}

More details can be found in the isolator section

## Troubleshooting

#### Gimbal tilt controls are reversed

{% hint style="info" %}
You can invert the gimbal tilt control under the camera settings
{% endhint %}

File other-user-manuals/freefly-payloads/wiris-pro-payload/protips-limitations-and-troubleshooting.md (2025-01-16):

# Protips, Limitations, and Troubleshooting

## First things first&#x20;

{% hint style="success" %}
The Wiris Pro Payload is supported in Astro firmware version 1.3.2 or later. Update your astro!
{% endhint %}

{% hint style="info" %}
Make sure to update AMC to the latest version too!
{% endhint %}

{% embed url="https://freefly.gitbook.io/astro-public/astro/maintenance-manual/software" %}

## #Protips

{% hint style="success" %}
Slow speed mode makes the gimbal easier to precisely control when zooming in.
{% endhint %}

&#x20;Learn about it under the [Precise Gimbal Control](https://freefly.gitbook.io/astro-public/astro/payloads/wiris-pro-payload/operating-handbook/precise-gimbal-control) section

{% hint style="success" %}
If you want images to be geotagged, insert a USB thumbdrive in Astro and set the image storage mode to 'External USB'
{% endhint %}

{% hint style="warning" %}
Be careful not to become disoriented when flying with the camera zoomed in. We recommend resetting the camera zoom to 1x before flying to a new inspection location.
{% endhint %}

## Limitations

#### Gimbal

{% hint style="warning" %}
Do not hotswap or plug in the gimbal when the aircraft is powered on. This can damage the aircraft or gimbal
{% endhint %}

{% hint style="warning" %}
Make sure you are using the correct vibration isolator
{% endhint %}

More details can be found in the isolator section

#### Wiris&#x20;

{% hint style="info" %}
The Wiris Pro takes about 3 minutes to fully calibrate the thermal sensor. You can still use the camera right after boot, but temperature readings may be slightly off
{% endhint %}

{% hint style="info" %}
Make sure to eject the Wiris drive from you computer before unplugging the cable. Power cycle the aircraft and gimbal before capturing any additional video or photos.&#x20;
{% endhint %}

{% hint style="info" %}
The video feed may stop after disconnecting from a PC. This is normal, the video will resume after a reboot of the aircraft
{% endhint %}

{% hint style="danger" %}
**Do NOT format the SSD of the Wiris Pro when connected to a PC. This can brick the camera and will require it being sent back for repair.**&#x20;
{% endhint %}

Check out the [Formatting Media section](https://freefly.gitbook.io/astro-public/astro/payloads/wiris-pro-payload/operating-handbook/downloading-formatting-media) for more info

## Troubleshooting

#### Video doesn't come up

{% hint style="info" %}
Occasionally, we have observed that the Wiris Pro gets 'stuck' during bootup. If you are having trouble getting connecting to the camera, check status light on the back of the camera. If the camera has flashing red/blue lights or a solid red light, this is likely the case. In our testing, rebooting the aircraft resolves this issue.&#x20;
{% endhint %}

#### IR video is black

This can happen if the thermal exposure is set very far off from what the camera is looking at.&#x20;

{% hint style="info" %}
Set the thermal exposure mode to auto or adjust your exposure temperature in the camera settings menu
{% endhint %}

#### Gimbal tilt controls are backwards

{% hint style="info" %}
You can invert the gimbal tilt control under camera settings
{% endhint %}

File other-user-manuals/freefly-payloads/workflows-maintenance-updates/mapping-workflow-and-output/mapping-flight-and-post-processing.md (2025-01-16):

# Mapping Flight and Post Processing

{% hint style="warning" %}
DIU Blue Astros come with stealth logging enabled, which stops GPS data from being written to imagery and logs. [Stealth logging must be disabled](https://freefly.gitbook.io/astro-public/other-user-manuals/ecosystem/diu-blue-suas#logging) to allow GPS data to be written for mapping workflows
{% endhint %}

### Esri Site Scan

Astro is integrated with Esri's [**Site Scan,**](https://www.esri.com/en-us/cp/site-scan-for-arcgis-3d-drone-mapping-software/overview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\&aduc=Advertising\&aduca=UR-Drone\&aduco=other\&adum=PPC\&adusf=Google\&adut=ppcbrand\&sf_id=7015x000001PMIkAAO\&utm_source=Advertising\&ef_id=Cj0KCQiAsburBhCIARIsAExmsu6Bz5S-BWpIf-yzE8ZTh0jpWc_7RUE8k6KVhOnPssNdTJuMVpl6zzcaAmWCEALw_wcB:G:s\&s_kwcid=AL!8948!3!633156847152!e!!g!!esri%20site%20scan&_bk=esri%20site%20scan&_bt=633156847152&_bm=e&_bn=g&_bg=143683278632\&aducop=esri%20site%20scan-e\&gclsrc=aw.ds) allowing for a very clean end-to-end mapping process that we cover in the [**Site Scan section of our wiki**](../../../ecosystem/esri-site-scan/). We strongly recommend using Site Scan if your primary use case for Astro is mapping.&#x20;

### Flying

From AMC Fly view, use the confirmation slider to begin a mission.&#x20;

During a mission, you can take control of the aircraft pressing the Flight Mode buttons on the controller (Position, Altitude, and Manual). The aircraft will switch to the selected flight mode and begin responding to your commands.

Verify that the camera is oriented correctly (downward when taking photos and forward when landing to avoid ground strikes).

Verify that the aircraft is taking photos by looking for photo icons on AMC Fly view map or the incrementing photo counter on the live video camera control panel.&#x20;

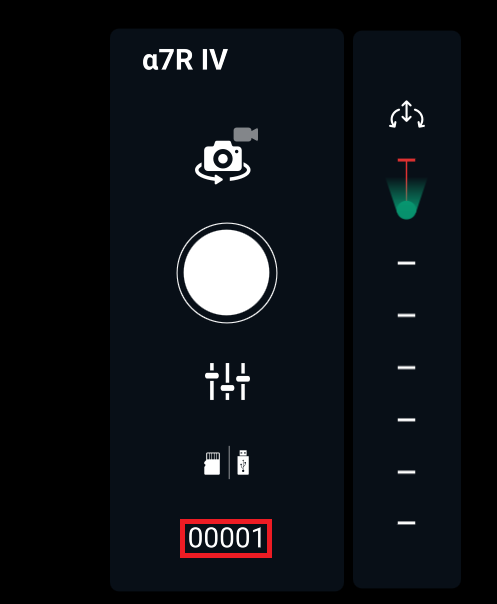
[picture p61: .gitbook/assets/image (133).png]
Camera counter is visible while previewing the video feed on the Herelink


### Landing

When the aircraft lands, do not immediately power down. The aircraft will automatically perform post-processing operations like creating the RINEX observation files. AMC will show a progress bar. When the process is complete, the drone may be powered down. \
\
The drone can be folded and moved while it is doing its post-processing, but it is suggested to disconnect ONE battery as an added safety measure. Do not disconnect the payload while the aircraft is powered on.&#x20;

### Post Processing

Astro Map output is compatible with modern stitching software that can accept normal JPEG EXIF Geotags. In general, if it can use the files generated by a DJI Phantom 4 RTK, it will work with Astro photos. Freefly has tested the following for compatibility:

* [ESRI Site Scan](https://www.esri.com/en-us/arcgis/products/site-scan-for-arcgis/overview)
* [Pix4D](https://www.pix4d.com/)
* [Drone Deploy](https://www.dronedeploy.com/)
* [Propeller.aero](https://www.propelleraero.com/)

## High Accuracy Workflow

This section focuses on tools and techniques to improve accuracy.

**Relative Accuracy** describes the quality of measurements between points within a map (e.g. object size, shape, and separation). The map may not be aligned with the real world, but it is self-consistent (lengths of objects are accurate).

**Absolute Accuracy** describes the quality of measurements between points on a map and points in the real world.

### GSD

Ground Sample Distance (GSD) is the photo or map's "resolution" typically given in units of distance per pixel, e.g. cm/px. GSD is the size of the camera's pixels on the ground.

Functionally, GSD is the upper limit of precision for measurements extracted from a photo/map/cloud/mesh. For example, if a measurement precision of 1 cm is needed, the mission should be planned so that GSD is 1 cm or less.

GSD can be chosen as a survey input in AMC's Plan tab, but it will adjust the altitude of the mission using the given overlap requirements. It is important that the operator verify the resulting altitude that AMC calculates is safe to fly.&#x20;

### Coordinate Systems

The cheapest accuracy available is in eliminating coordinate system errors. It's not always easy, but it is free.

Post-processing software is designed to accept input in a variety of coordinate systems, but each piece of software has its own peculiarities in handling coordinate conversion. Here are a few tips:&#x20;

* Astro outputs photos geotagged in WGS84 latitude/longitude, and EGM96 elevation in meters. This is what is found on the USB stick plugged into the aircraft.
* When working with PPK, coordinate systems become much more complicated. The coordinate system the photos are in after PPK will be the SAME as the coordinate system used by the base station. For example, if the base station was placed on a pre-surveyed marker, and you know the coordinates of that marker in NAD83(2011) geographic coordinates, and those are what you enter as the base station position in the PPK app, then all the resulting geotags from the PPK app will ALSO now be in NAD83(2011).&#x20;
* A common error is when the base station location is corrected using an online service such as OPUS. Those services accept the base station observation file and solve for the position of the unit with high accuracy. However, the reported position coordinate system may not match the desired output at the survey site. OPUS reports back in IRTF2014 and NAD83(2011). Use the base coordinates that apply to your site. If your site is not using any of those, Tools like NOAA's [VDatumWeb ](https://vdatum.noaa.gov/vdatumweb/)can convert between them.&#x20;
* The FreeflyPPK app or Precise Flight PPK app does not include vertical datum settings. (Look for these in a future version.) The resulting vertical reference will match the coordinates of whatever height is used for the base station.

### Geotag Corrections

The photos created by the Mapping Payload are geotagged when they are stored on a USB drive (not the SD card in the camera).

Geotags are metadata attached to photo files that capture the camera's location in the 3D space and the direction vector of the camera when the photo was taken. These pieces of information allow post-processing software to quickly perform an initial alignment of the photos. More accurate geotags make processing time shorter and improve the quality of the output.

Astro will geotag the photos with whatever level of accuracy is available to the aircraft. The onboard GPS provides absolute accuracy down to 1-3 meters. The relative accuracy will be much higher, but it depends on the GPS constellation, mission duration (it drifts over time), and other factors.

The accuracy of GPS systems can be improved by strategies involving multiple receivers.&#x20;

If a Freefly RTK Base Station is connected, the geotag _absolute accuracy_ does not improve (unless placed on a previously known location), but _relative accuracy_ is refined to the centimeter range.

Astro stores onboard GNSS observations and the geotag accuracy (both relative and absolute) can be improved further by post-processing after the fact. This process is known as "PPK". Freefly and Auterion both have apps that can correct the photos via PPK and improve their absolute accuracy to as good as 1-3cm.&#x20;

PPK processing can be performed with a variety of base stations and software. The next section gives more detail.

### PPK

{% content-ref url="ppk-software.md" %}
[ppk-software.md](ppk-software.md)
{% endcontent-ref %}

The easiest way to increase absolute accuracy is to use a GNSS Base Station with [Astro's free PPK Software](ppk-software.md#freeflyppk). PPK Software uses GNSS Base Station output to improve photo geotag accuracy through a process called Post Processed Kinematic (PPK) correction. Accurate geotags give your post-processing software a better starting point, improving output map/cloud/mesh accuracy.

How accurate is PPK? Relative accuracy typically is less than 1cm. Absolute accuracy is more complicated:

If no other corrections are used (i.e. no GCPs) absolute accuracy is the same as that of the base station. PPK essentially solves position offsets by comparing the aircraft's position to the base station, so if the base station position is known globally accurate to 2cm, the resulting PPK geotags will be similar.&#x20;

These are a few ways to determine base station location, ordered from highest to lowest accuracy:

* Place GPS base station precisely on a known ground control point survey marker using a high-accuracy tripod with tribrach. A survey pole and tripod can also be used, but accuracy might suffer depending on how accurately the pole in question can be leveled.&#x20;
* Place the GPS in a clear view of the sky and leave it running for an hour or more. Then use an online post-processing tool such as [NGS OPUS](https://geodesy.noaa.gov/OPUS/) or [Trimble Centerpoint RTX](https://www.trimblertx.com/uploadform.aspx) if you have a Trimble base station. This will take all the observations from the GPS and do its own PPK processing to determine the location of your GNSS unit very accurately. The downside is often having to wait hours or days for the underlying GPS data to be updated in OPUS before it will process your file. (Pay attention to the [coordinate system](mapping-flight-and-post-processing.md#coordinate-systems) that is returned)
* Average the position file generated by your GPS unit- if it's been stationary for over an hour, reasonable accuracy can be achieved, although GPS can vary slowly over many hours so this still may have sub-meter errors.&#x20;
* Survey-in the GNSS; this usually integrates for a few minutes when it's powered on, then writes its averaged position to the RINEX headers. This value is better than nothing.&#x20;
* Read out the instantaneous position of the GNSS after you've set it up and it has achieved a stable lock. This is the least accurate, and will only be accurate to GPS's normal accuracy of 1-3m.&#x20;

#### An example PPK workflow:

1. Arrive at the site where you intend to fly.&#x20;
2. Set up base station, ideally, on a known survey marker. Otherwise, find an open space with a clear view of the sky (to the best of your ability).&#x20;
3. Start observation file logging on the base station. Many can be configured to start at power on, but it is usually worth checking that the base station is recording before takeoff.
4. Prepare Astro and fly missions.&#x20;
5. When you are done, log into the base station and stop recording.&#x20;
6. Download the RINEX files from the base station and put them on the USB drive from Astro.&#x20;
7. Geolocate the base station. If it was on a known point, you're ready to go. If you are using an online processing tool, wait until the base station has enough data from nearby CORS sites to process (1-2 hours minimum), then get the processing report. Acquiring this report varies depending on your hardware and location, so consult the user manual of your base station for more info.&#x20;
8. Use the FreeflyPPK app or the Auterion PreciseFlight app to post-process the photos.
9. Take the resulting high-accuracy geotagged photos to whichever photogrammetry tool you choose (ESRI sitescan, pix4d, DroneDeploy, propeller.aero, Agisoft, etc).

### GCPs - Ground Control Points

Ground Control Points (GCP) are pre-surveyed points that are marked to be visible in aerial photos. GCPs are used by the post-processing algorithm to correct distortion and align the map with the real world.&#x20;

PPK allows you to achieve high-accuracy maps that do not require GCPs. GCPs can require significant effort to survey and process. However, they tend to be the most accurate, even with poor initial coordinates in the photos.

GCPs can be used in a number of ways:

* A base station can be placed on a single GCP and used as high-accuracy positioning for PPK processing. This is the method that gives great results for the lowest amount of effort.&#x20;
* A few GCPs can be used, one with the base station. This allows high-accuracy PPK, and the additional GCPs can be used as an accuracy check on the PPK results.
* a large quantity of GCPs (5+) can be surveyed and used in combination with or in lieu of PPK. This is the most costly as it requires surveying all the points, and then running the tagging process.&#x20;

Maps using GCPs will generally be as accurate as the GCP can be marked in the photos and how accurate the GCP coordinates themselves are known (usually reported by your surveyor).&#x20;

GCPs are used like this: Before flying, ensure that the mission will overfly multiple GCPs and ensure their clear visibility in aerial photos. After flying, enter GCP coordinates into your post-processing software. Use your photogrammetry software's workflow to mark the locations of the known coordinates in the photos. Then there will be a processing step. Afterward, you can overlay the GCP checkpoints and measure the distance from their coordinates to the marker in the output.

GCPs can be established by a surveyor, or with your GNSS base station.

* Propeller: [https://www.propelleraero.com/blog/how-to-optimize-your-ground-control-point-placement/](https://www.propelleraero.com/blog/how-to-optimize-your-ground-control-point-placement/)

Astro is compatible with Propeller Aeropoints.

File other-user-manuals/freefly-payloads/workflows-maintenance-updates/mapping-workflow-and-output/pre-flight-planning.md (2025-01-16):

# Pre-flight Planning

## Weather

Weather is a big driver of how good the resulting maps will be. Because of lens limits and the requirement for high shutter speeds to reduce motion blur, maps are best when taken with bright light. The best results are around noon when the sun is directly overhead and casting few shadows; a bright, overcast day also works well for similar reasons.&#x20;

When ambient light is low due to heavy clouds or in the evenings, the camera will expose the scene but will have to increase ISO to get reasonable exposure. Beyond ISO 1000, noise and blur from the denoising filter in the camera will start to impact photo quality.&#x20;

If light conditions are low, the shutter speed can be reduced. However, the drone will need to fly slower to ensure no motion blur. The camera lens is sharpest above f/5, but the aperture can be opened up to provide more light. Some lens artifacts and blurring around the edges may be present with a wider aperture/lower f-stop.&#x20;

Additionally, flying over wet surfaces may cause problems for photogrammetry workflows. It tends to make asphalt very dark, which can cause stitching software to have a hard time, and reflective surfaces can't be used to stitch photos.&#x20;

## Download Maps for Offline Use

AMC caches recent maps. To make certain that maps for a specific location are stored on your remote controller before you go to a site with no internet, download them while the remote controller is connected to wifi.&#x20;

{% tabs %}
{% tab title="Video" %}
{% embed url="https://www.loom.com/share/ec5622167e7141d0883f4b5aec341b0f" %}
{% endtab %}

{% tab title="Text" %}
Tap the Herelink icon in the top-left corner of AMC, select Settings, and select Offline Maps. Select "Add New Set".&#x20;

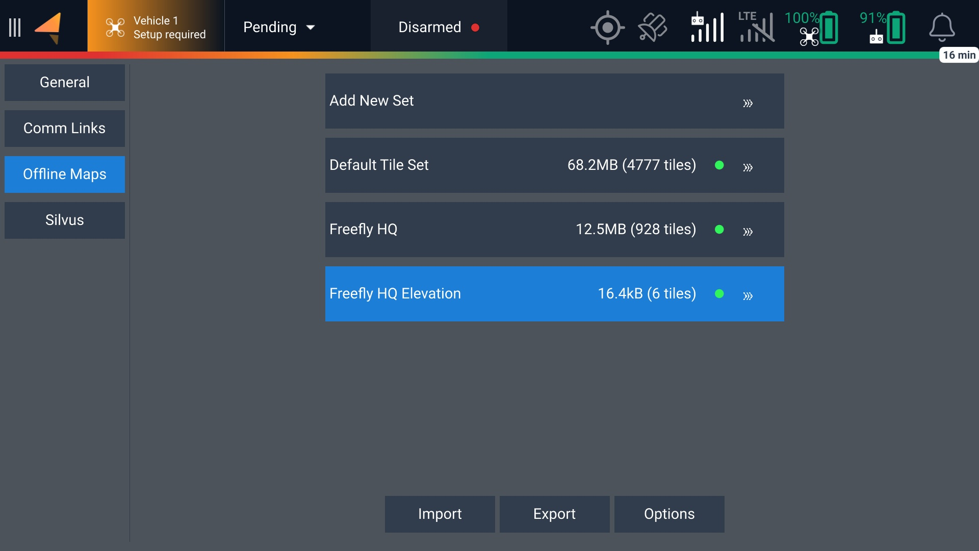
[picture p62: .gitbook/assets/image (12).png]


Offline maps gather satellite data from the selected source (in this case, Bing Hybrid maps) and download tiles to make up the map in up to two different zoom levels. The higher the zoom level, the better the quality of the image and the more tiles it will take to cover the area framed by your screen.&#x20;

As such, high zoom levels of large areas can lead to very large file sizes. Lower zoom levels are recommended for large areas, and higher zoom levels will result in better offline maps for smaller areas. After adjusting the map to your preferences, you can select Download.&#x20;

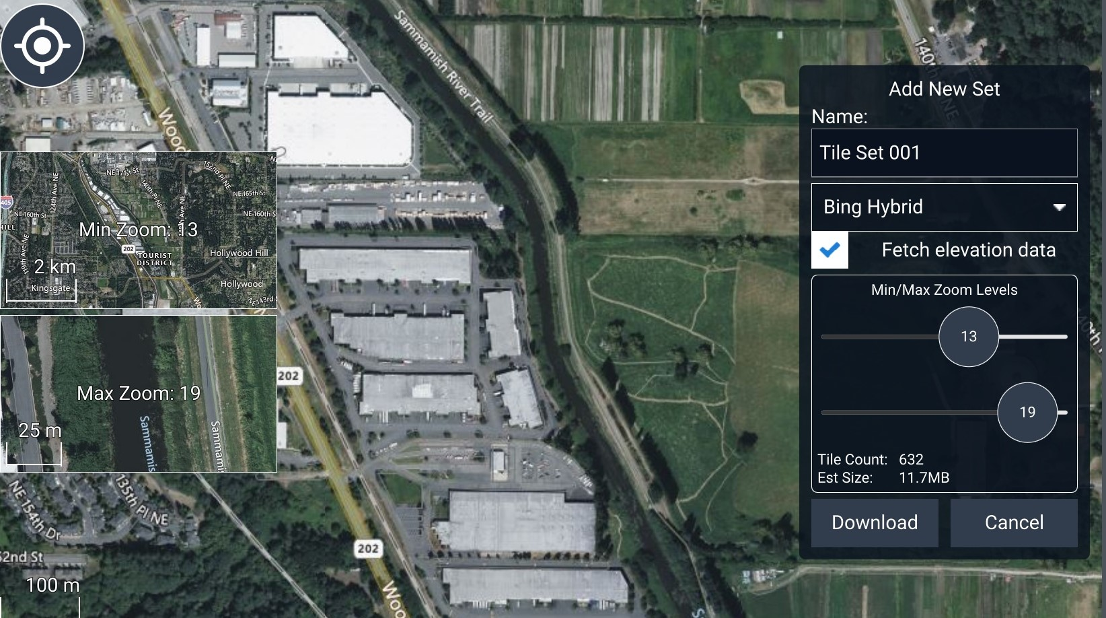
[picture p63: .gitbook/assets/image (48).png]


After the map is downloaded, you can view it from the Offline Maps page. Any missions in the area on this map will show the satellite images even if you are not connected to the internet, and if the "Fetch elevation data" option was selected you will also have the option to view the terrain height while planning your mission.&#x20;

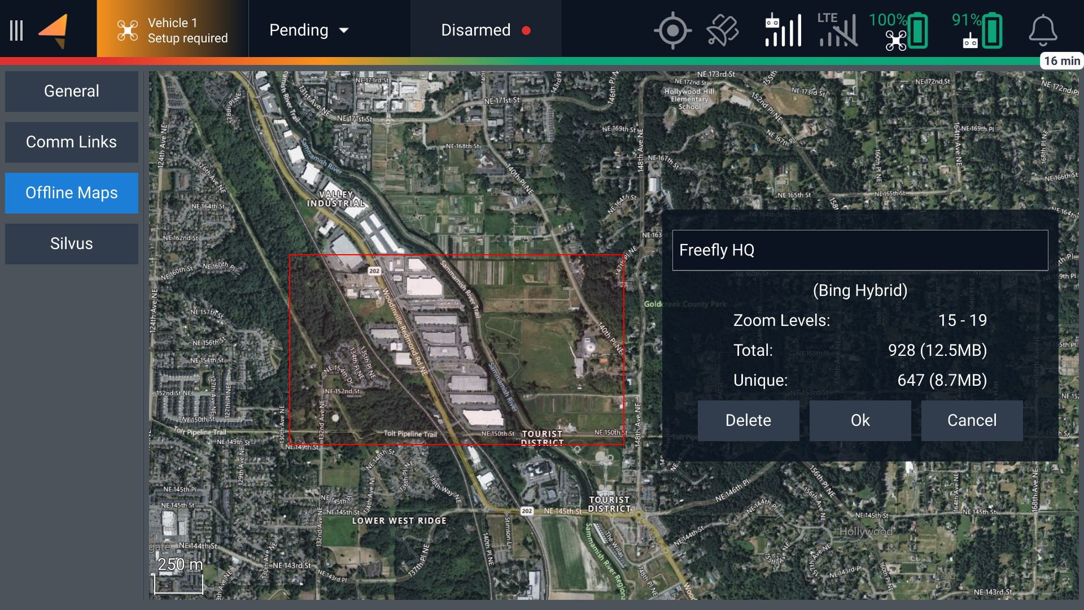
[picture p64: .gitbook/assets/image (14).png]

{% endtab %}
{% endtabs %}

## Plan a Mission

{% hint style="warning" %}
DIU Blue Astros come with stealth logging enabled, which stops GPS data from being written to imagery and logs. [Stealth logging must be disabled](https://freefly.gitbook.io/astro-public/other-user-manuals/ecosystem/diu-blue-suas#logging) to allow GPS data to be written to photos
{% endhint %}

1\. Figure out the minimum safe flying altitude at your site (i.e. above obstacles and giving a good line of sight). Enter this value in AMC > Vehicle Setup > Safety > Return Altitude.

2\. Open the camera view for the payload, and select the settings  icon. Select the lens that matches what you're using (default 24mm).

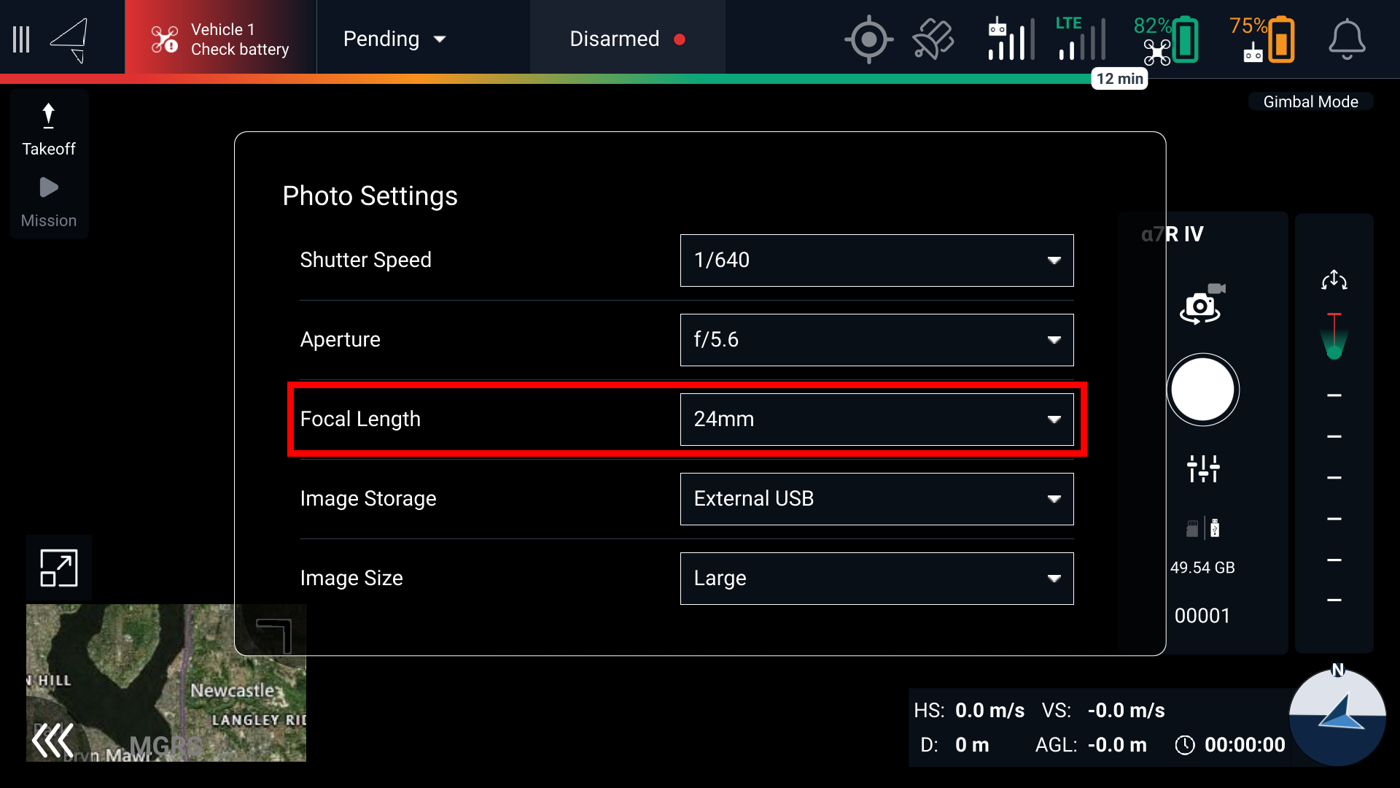
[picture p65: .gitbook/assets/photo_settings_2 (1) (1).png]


3\. Open AMC Plan view, and select "Pattern" in the left sidebar (creates flight path that covers the site and automatically triggers photos). Choose a pattern type and shape and it'll appear on the map. Don't detail the shape yet- We'll come back to that.

4\. In the Pattern/Survey waypoint settings, open the Camera tab, and select Preset: Sony ILX-LR1 - 24 mm SIGMA.

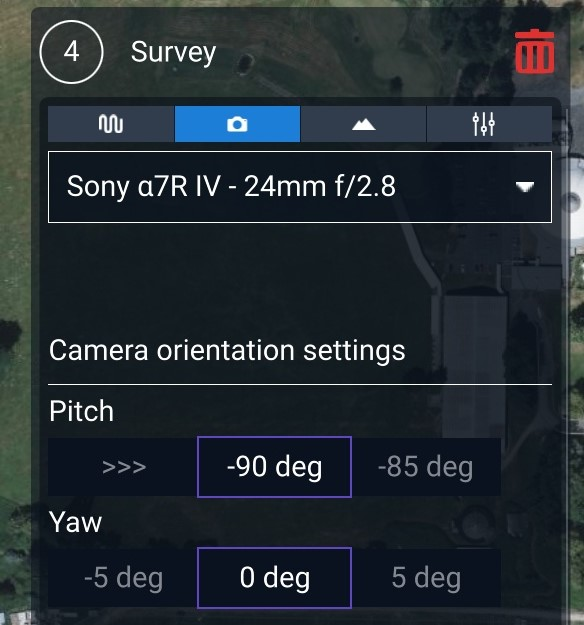
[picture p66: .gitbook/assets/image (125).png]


5\. Set Altitude. Start in Pattern waypoint settings and enter the minimum safe value from step 1. Check the Ground Sample Distance (GSD) value at the bottom of Pattern Waypoint settings. If GSD is smaller than your needs, increase altitude to increase GSD. Then go to Mission Waypoint settings and enter the same altitude.

6\. Turn on Terrain Display by selecting the square T button in the bottom-left corner. Check the heightmap to make sure the flight path clears the terrain by a comfortable margin.&#x20;

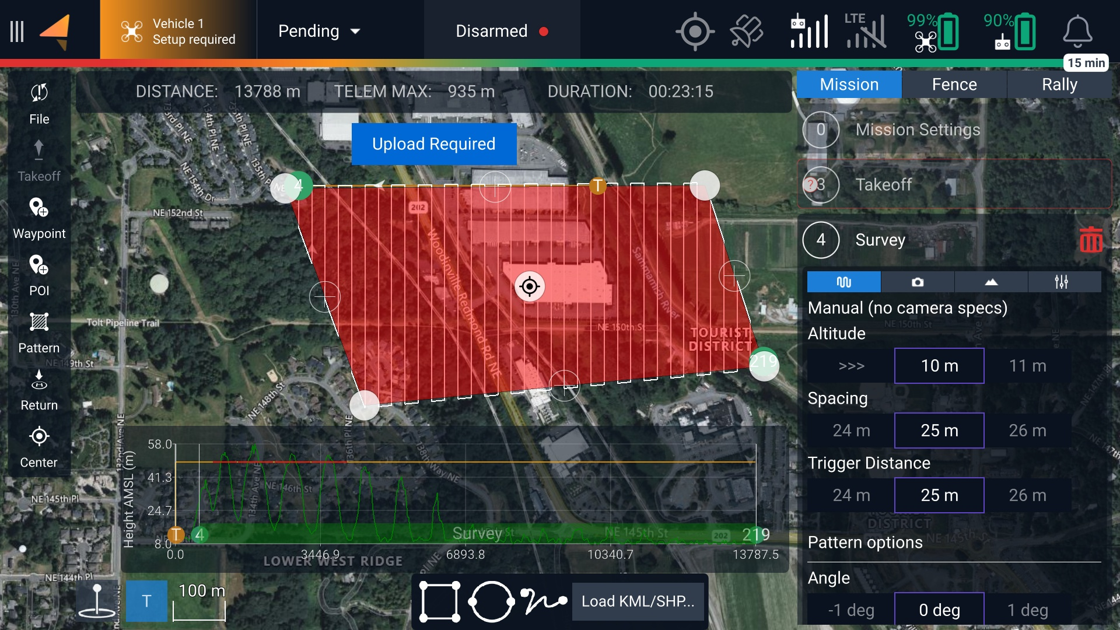
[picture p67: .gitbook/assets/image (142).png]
Height map at the bottom shows terrain in the area is higher than the mission altitude.


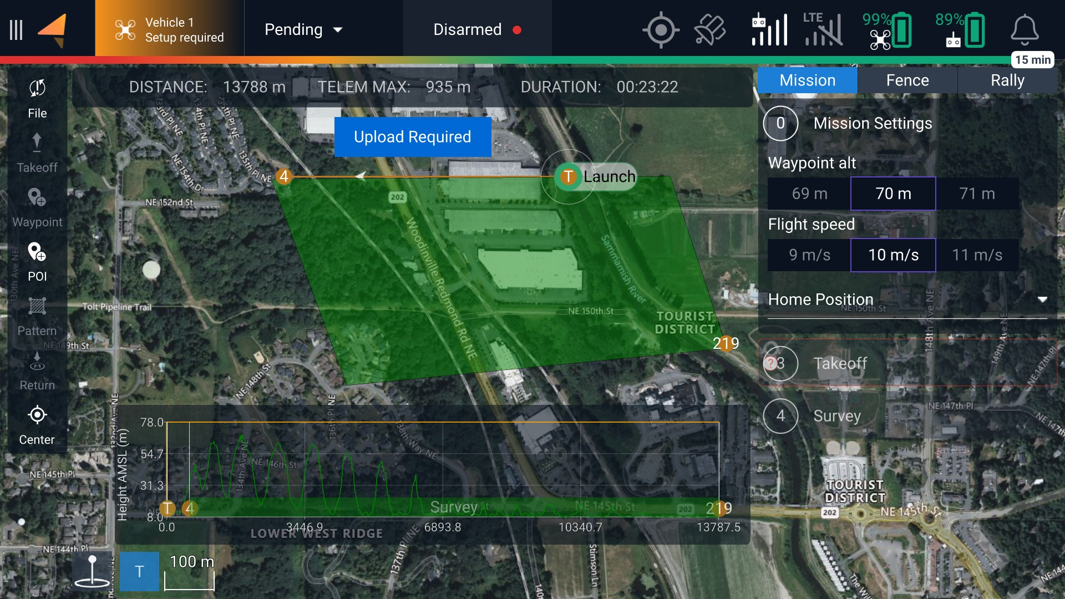
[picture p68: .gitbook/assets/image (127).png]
Altitude of the mission was increased from 50m to 70m, avoiding the terrain.


7\. Set speed. Check the Photo Interval value at the bottom of Survey settings along the right. This interval needs to be 2 seconds or more. If it's less, decrease the mission flight speed or increase forward overlap (if this is acceptable for your mission). If the photo interval is larger than 2 seconds, you can optionally increase your flight speed.&#x20;

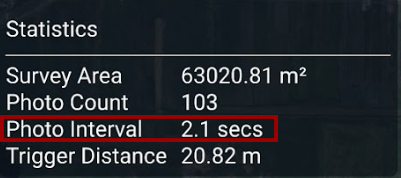
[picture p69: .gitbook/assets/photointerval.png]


8\. Adjust the Pattern area. Make sure the green area (the area to be flown and photographed) is larger than the map you need. Make the green area larger on every side by at least the width between flight passes. Note the estimated flight duration at the top of the screen. If the duration is longer than 23 minutes, it's likely to require a second flight.&#x20;

9\. Add a Return waypoint command if you want the aircraft to come home and land when finished. This is optional but recommended. If the mission's last command is a Pattern or Waypoint, AMC will not notify you that the mission has ended. The aircraft will hover at the last waypoint, likely until the battery failsafe is triggered and Astro returns home automatically.&#x20;

If these instructions are unclear or if you have any additional questions, you can learn more about planning in the[ AMC docs](https://docs.auterion.com/auterion-mission-control/plan) or contact us at support@freeflysystems.com.

{% embed url="https://www.loom.com/share/b973a6ad892a4d01a224fdd156a42f60" %}
Simple mission workflow
{% endembed %}

### Coverage

To get high-quality results, every area of interest in the map should appear in 5 or 6 overlapping photos. Obtaining this much coverage along edges or in corners requires that the area to be flown is larger than the area to be mapped. Also consider that if the gimbal is not pointing straight down (for crosshatch surveys and such), the drone will need to fly PAST areas that need to be seen in images because the image is looking in front of the drone.

## USB Setup

The USB flash drive included will be formatted to work with Astro. In the event that you encounter issues or would like to use a different USB flash drive with Astro, follow the instructions in the USB formatting section. Be sure enough space is available; you will need at least 16GB for a single mission.

{% content-ref url="../usb-formatting.md" %}
[usb-formatting.md](../usb-formatting.md)
{% endcontent-ref %}

### Included USB Flash Drive

[Astro Map](https://store.freeflysystems.com/products/astro-map) and the [mapping payload ](https://store.freeflysystems.com/products/mapping-payload)both include a [Samsung 64GB flash drive](https://semiconductor.samsung.com/us/consumer-storage/usb-flash-drive/type-c/). If you want to replace or purchase additional flash drives, we recommend trying to get the same model as we have tested this drive thoroughly. It will also help our support team troubleshoot any issues you might encounter.&#x20;

## Camera Setup

#### Camera body and 24 mm lens settings

* Body Exposure Compensation Dial: 0, and the lock button engaged

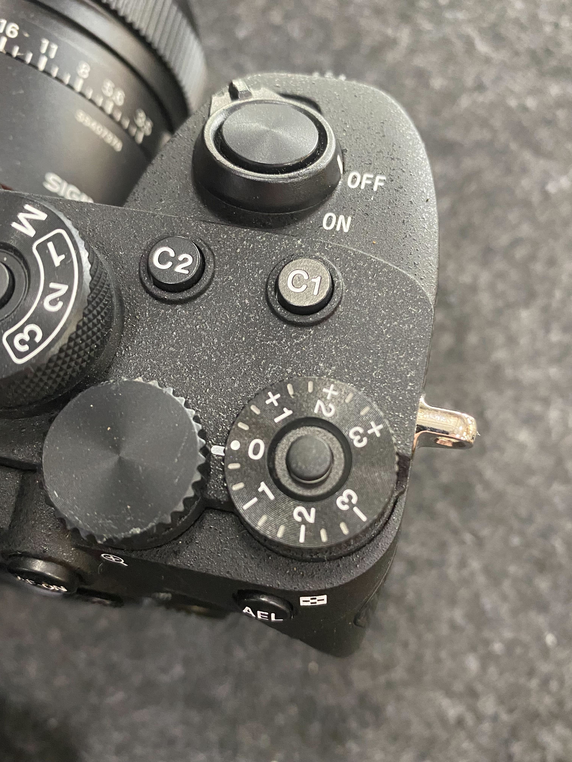
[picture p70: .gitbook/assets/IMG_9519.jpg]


* Lens Aperture ring: A&#x20;

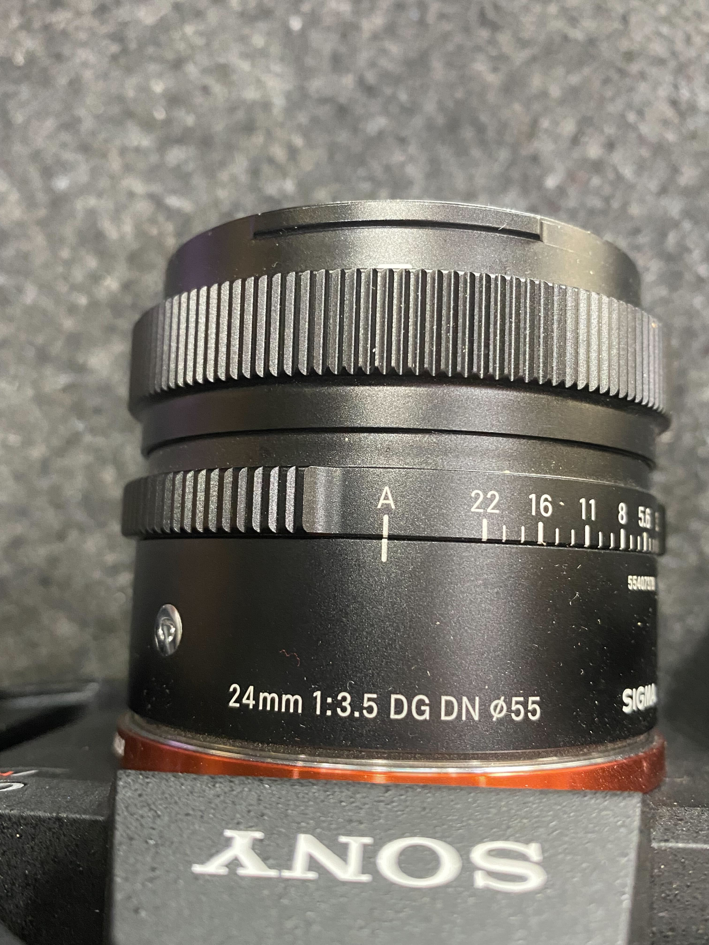
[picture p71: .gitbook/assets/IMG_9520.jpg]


* Lens Focus switch: AF

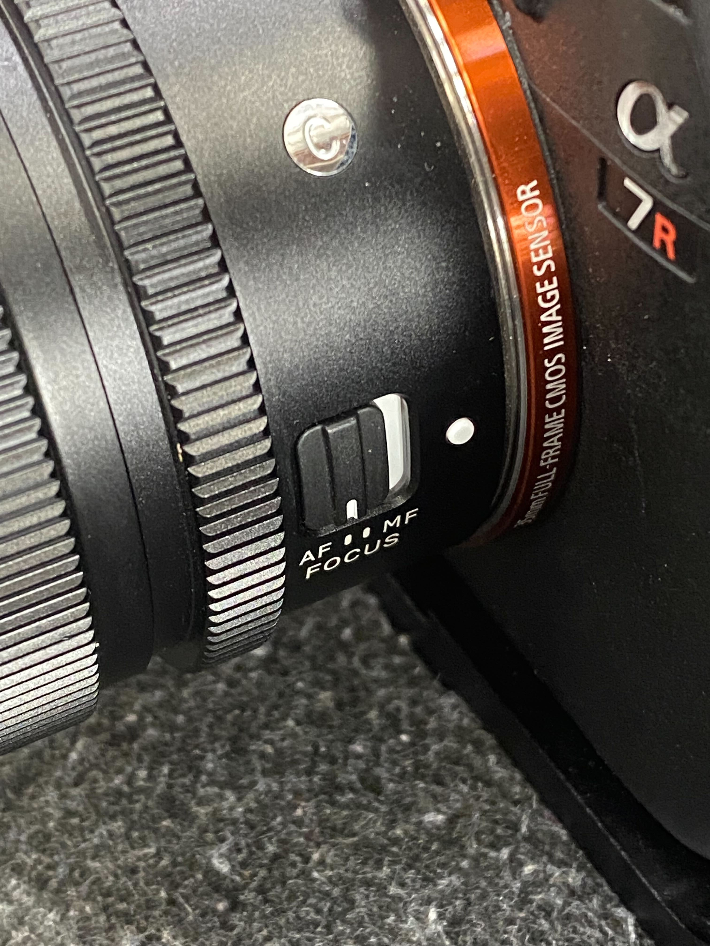
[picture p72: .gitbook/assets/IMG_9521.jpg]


#### AMC camera settings (tap slider icon below on-screen shutter button)

* Focus: Auto (infinity does work as well)
* Exposure Mode: Manual
* ISO: Auto
* Aperture: f/5 - f/11 depending on lighting conditions
* Shutter: 1/1000 or greater (can go as low as 1/500 but aircraft needs to slow down to prevent blur.
* Storage: USB Drive

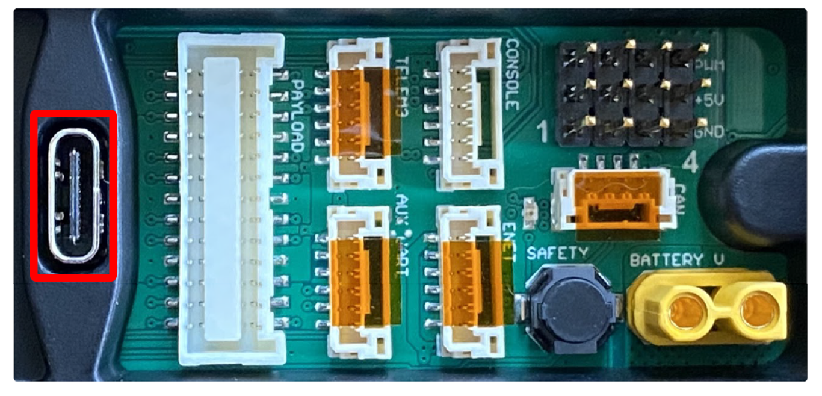
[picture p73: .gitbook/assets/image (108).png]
The USB drive should be plugged into the USB-C port near the IO panel on the bottom of Astro.


{% hint style="info" %}
When light is low (e.g. dark cloudy day), we need to adjust the shutter speed and aperture to avoid an excessive increase in the ISO sensitivity. The first step is to open the aperture. If an aperture of f/5 is still not bright enough, the second step is to decrease shutter speed. Working in this order keeps shutter speed as high as possible to minimize motion blur. If shutter speed must be reduced and motion blur is seen, reduce flight speed.\
\
Wider apertures than f/5 can be used, but the photos will lose sharpness, so be sure to test if the quality of the resulting images will satisfy the needs of your mission.&#x20;
{% endhint %}

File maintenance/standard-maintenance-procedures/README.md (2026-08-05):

---
icon: wrench
---

# Standard Maintenance Procedures

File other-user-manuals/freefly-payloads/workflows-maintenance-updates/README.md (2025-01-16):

# Workflows/Maintenance/Updates

Integrated payloads developed by Freefly share much of the same information for updating gimbal firmware, isolator configurations, workflow tips, and formatting storage devices. Payload specific workflows, information, and settings are covered in the above sections.

## Workflows

{% content-ref url="mapping-workflow-and-output/" %}
[mapping-workflow-and-output](mapping-workflow-and-output/)
{% endcontent-ref %}

{% content-ref url="inspection-workflow.md" %}
[inspection-workflow.md](inspection-workflow.md)
{% endcontent-ref %}

{% content-ref url="precise-gimbal-control.md" %}
[precise-gimbal-control.md](precise-gimbal-control.md)
{% endcontent-ref %}

## Maintenance

{% content-ref url="usb-formatting.md" %}
[usb-formatting.md](usb-formatting.md)
{% endcontent-ref %}

## Updates

{% content-ref url="gimbal-firmware.md" %}
[gimbal-firmware.md](gimbal-firmware.md)
{% endcontent-ref %}

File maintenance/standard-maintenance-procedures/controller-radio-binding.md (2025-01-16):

# Controller / Radio Binding

**Pilot Pro (Herelink Radio)**&#x20;

* If you are upgrading your Astro from using Herelink GCS (Legacy) to Pilot Pro (Herelink Radio) for the first time, then your Astro needs an upgrade first. Please follow [these instructions](../../other-user-manuals/ecosystem/components/pilot-pro-controller.md#upgrading-astro-to-pilot-pro-controller-950-00140-02).

* If Astro was already upgraded to be used with Pilot Pro, then follow[ these instructions](https://freefly.gitbook.io/pilot-pro-public/operating-handbook/radio-modules/herelink-radio#binding).

**Pilot Pro (Doodle Radio)**

* [https://freefly.gitbook.io/pilot-pro-public/operating-handbook/radio-modules/doodle-labs-radio-module/doodle-binding-pairing](https://freefly.gitbook.io/pilot-pro-public/operating-handbook/radio-modules/doodle-labs-radio-module/doodle-binding-pairing)&#x20;

**Herelink GCS (Legacy)**

* [#herelink-binding](../../other-user-manuals/ecosystem/components/pilot-handsets/herelink-controller-maintenance/#herelink-binding "mention")

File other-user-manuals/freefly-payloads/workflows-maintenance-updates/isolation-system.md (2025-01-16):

# Isolation System

The Astro Isolator is recommended for all payloads, including the LR1, A7R4, Wiris Pro, and OGI Payload.&#x20;

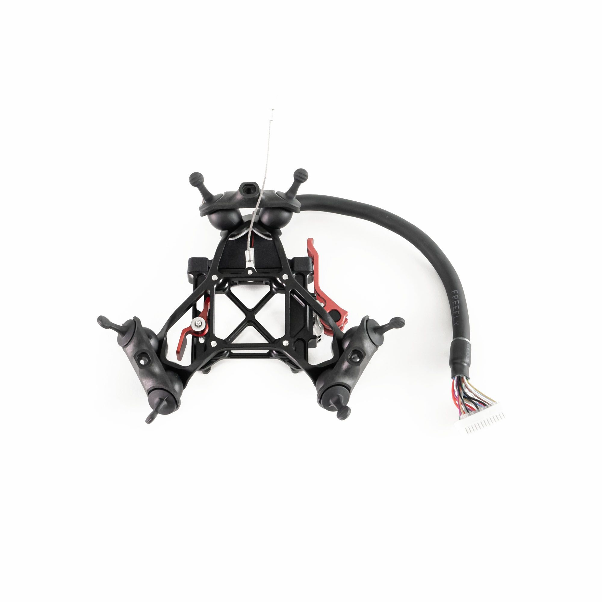
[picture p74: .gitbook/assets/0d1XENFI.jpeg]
<figure><figcaption></figcaption></figure>

{% embed url="https://www.youtube.com/watch?v=KoJAUCyK5_Y" %}

{% hint style="warning" %}
There are multiple versions of the isolator, check to make sure you have the correct version&#x20;
{% endhint %}

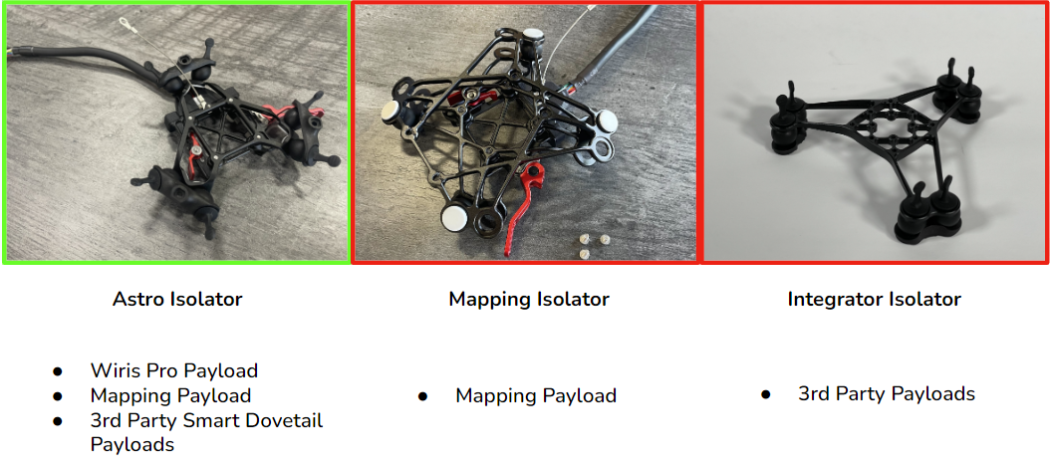
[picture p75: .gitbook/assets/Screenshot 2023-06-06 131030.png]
<figure><figcaption></figcaption></figure>

* The Astro Isolator is available[ in our store](https://store.freeflysystems.com/products/astro-isolator). Instructions on how to install the isolator on Astro are below:

{% embed url="https://freefly.gitbook.io/astro-public/astro/ecosystem/components/vibration-isolators" %}

This isolator has the Smart Dovetail connector attached and allows swapping between the OGI Payload, LR1 Payload, Wiris Pro Payload, A7R4 Payload, and other payloads that use the Smart Dovetail standard.&#x20;

{% hint style="info" %}
We recommend the Astro Isolator over using the isolator that came with Astro Map. The Astro Isolator is compatible with all payloads.&#x20;
{% endhint %}

Check all the dampers are in good condition before each flight, as these can wear out over time. We recommend replacing all dampers on the isolator every 6-12 months. 30A durometer damper replacements are included in the Astro Isolator Kit and are available through our store:

{% embed url="https://store.freeflysystems.com/collections/astro/products/astro-vibration-isolator-set" %}

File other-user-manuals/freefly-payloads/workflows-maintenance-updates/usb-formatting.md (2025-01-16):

# USB Formatting

### Recommended USB-C Flash Drive

* The LR1, A7R4, and OGI Payloads ship with this [**USB-C flash drive.** ](https://freefly.gitbook.io/astro-public/astro/payloads/astro-mapping-payload/operating-handbook/pre-flight-planning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)
* We recommend a USB 3.1 drive with a write speed above 50 mb/s.

{% hint style="info" %}
The USB thumb drive can slow down over time. This can propagate issues throughout the system. Fully [reformatting](https://freefly.gitbook.io/astro-public/other-user-manuals/payloads/astro-mapping-payload/maintenance-manual/usb-formatting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) the drive could help resolve this issue, but it is best practice to replace the flash drive if you are experiencing issues after a long period of use.&#x20;
{% endhint %}

### USB Setup

The USB flash drive included will be formatted to work with Astro. If you encounter issues or would like to use a different USB flash drive with Astro, format using the instructions below.&#x20;

## Formatting the USB Drive

#### Mac

1. Open Disk Utilities and click on the flash drive in the sidebar.&#x20;
2. Select the Erase option at the top of the window.&#x20;
3. In the Format dropdown, select MS-DOS FAT and click Erase.&#x20;
4. Once that completes, click the Eject arrow near your flash drive on the sidebar.&#x20;

#### Windows

1. Open This PC to show all connected drives.
2. Locate the USB drive you want to use with Astro, right-click on the image, and select "Format...". A small window should open.&#x20;
3. Select ExFat under the File System dropdown and click Start.&#x20;
4. Once that completes, right-click on the USB drive in This PC again and select Eject.&#x20;

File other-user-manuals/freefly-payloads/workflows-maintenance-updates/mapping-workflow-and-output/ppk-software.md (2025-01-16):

---
description: >-
  These free applications make it easy and simple to improve the accuracy of
  your survey through their use of Post Processed Kinematic corrections.
---

# PPK Software

## General Steps Before PPK Process:

If you are not able to follow these steps exactly, there is more guidance below.

1. Set up your base station (list of tested stations are below) and get it recording
2. Fly your mission with Astro, then wait for it to finish processing photos after landing
   1. Shutoff Astro
3. Pull USB-C stick, and insert into iPad (if accessing base-station data from iPad)
4. Go to Files app, browse to USB drive, and determine which folder has the files from this scan. i.e. folder 58
5. If using EMLID REACH:
   1. Open EMLID app:
      1. Stop logging all 3 logs (position, raw data, base correction)
      2. After they are zipped, download all 3 files to the usb stick in the same directory as the scan

## Freefly PPK

Freefly PPK Desktop Application takes photos and GPS data generated by Astro during a Mapping mission, as well as data from a GNSS base station, and applies the Post-Processing Kinematics (PPK) algorithm to tag photos with highly accurate geotags.&#x20;

**Download** the software from [https://freeflysystems.com/support/astro-support](https://freeflysystems.com/support/astro-support)

Current PC Version: v1.1.0 - Released 08/2024

Current Mac Version: v1.1.0 - Released 08/2024

**Table of Contents:**

1. Compatible Devices, Download Links
2. Input, Output, Workflow
3. Debugging tips if you encounter errors

### Compatible Devices

**Operating Systems**

* #### Windows PC - Tested on Windows 10
*   #### **macOS - Tested on M1 only**

    Note, for the current app version, you will need to override current mac security settings through instructions provided here: [https://support.apple.com/en-us/HT202491](https://support.apple.com/en-us/HT202491)

#### GNSS Base Stations

* Trimble R2,10,12
* Emlid RS2
* Generally, any device that can output RINEX (Observation and Navigation data files)

### Input

{% hint style="info" %}
**Important Tip: PPK process and upload to mapping software is 10x faster if you have the files in your local storage instead of thumb drive**
{% endhint %}

* Output folder from High Res Mapping Payload.
* RINEX files (OBS and Nav Data files) from GNSS base station _(that was actively recording GNSS data for the full duration of the time that the Astro mission was running)_.
* GNSS base station coordinate
  * Using pre-surveyed point as reference coordinate
  * Using Reference Network calculation (i.e. NOAA's CORS, Washington state's WSRN)&#x20;
  * For very basic results, averaged value from base station rinex file

### Output

Photos in PPK\_Photos folder with corrected geotags.&#x20;

### Workflow

{% hint style="info" %}
Updated 2022-06-01
{% endhint %}

**PRE-PPK CHECKS**

1.  As summarized above, to start PPK-ing your photos to get centimeter level geotag accuracy, you need to:

    * Complete an Astro Map mapping mission that writes photos, imagelog.json, \*capture.obs, and \*capture.json file into a mission folder (see Fig 1 below) into the USB-C thumb-drive. This is a simple and streamlined process, and you will generate this folder if you follow with the instructions in Astro Mapping Payload: Quick Map Workflow.

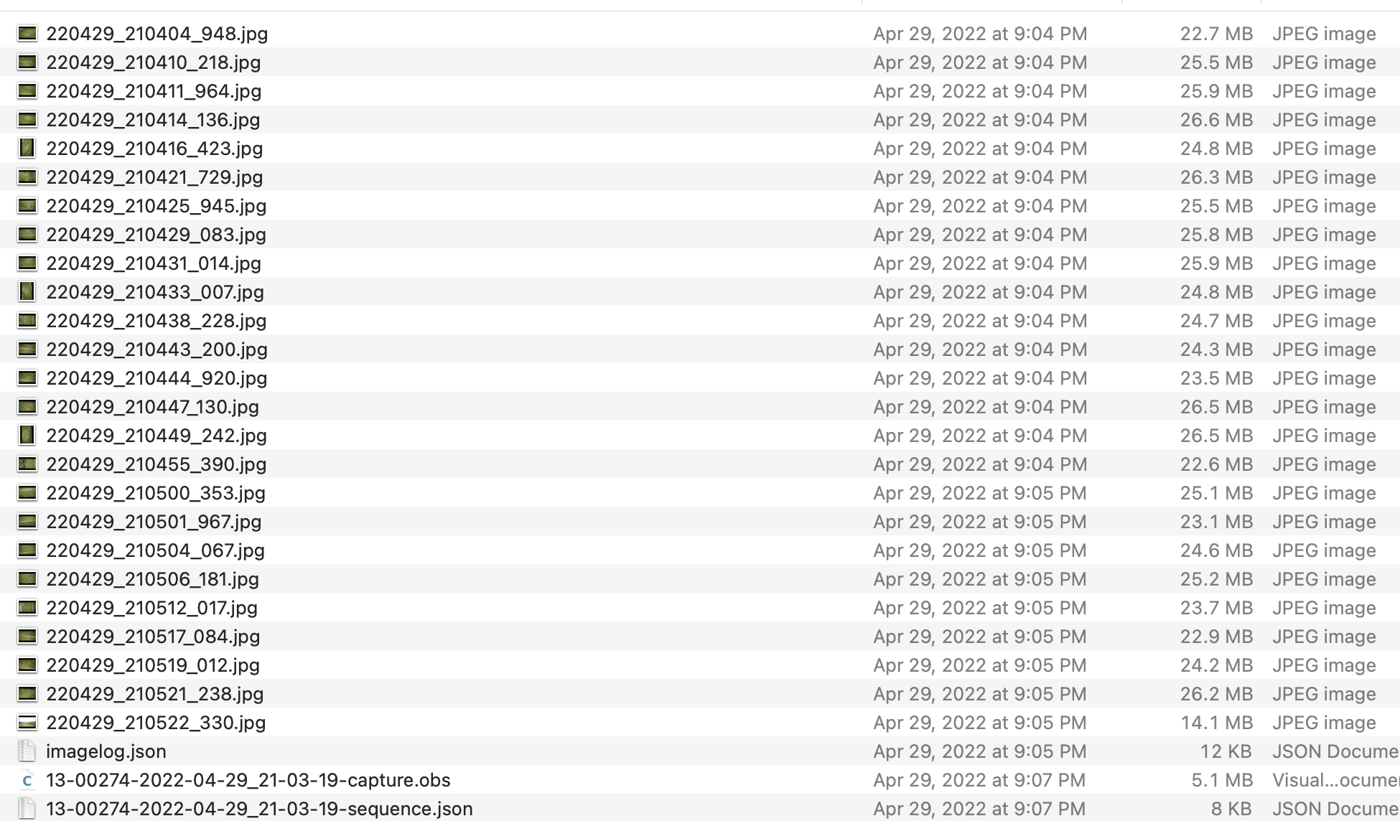
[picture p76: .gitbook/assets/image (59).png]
    

_Fig 1. Here is what the mission folder generated by an Astro Map mission might look like:_

* Have a GNSS base-station running and recording satellite data throughout the duration of the flight that can produce (Observation and Navigation data files). Grab the RINEX data files (usually ends with .<##>O - for OBS or .<##>P for NAV, sometimes just .RNX for both file types). If the file names are ambiguous, you can inspect the files and look at the first few lines to see if they contain the keywords Observation (for obs file) or Navigation (for nav file) data file. **IMPORTANT - Ensure that the NAV data file is a "MIXED NAV" data file that contains nav data for all constellations.**&#x20;

1. Grab the Observation and Navigation data files (either individually) or the folder that contains them and place it into the Astro Map mission folder that contains the photos and the other mapping mission artifacts (imagelog.json, \*capture.obs, and \*capture.json).

Placing base station file into the folder shown below:

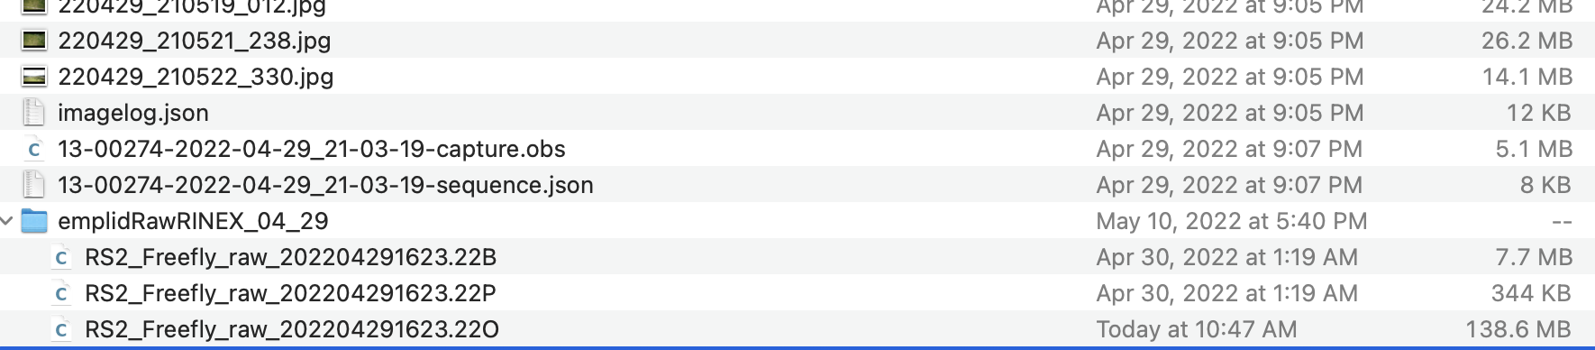
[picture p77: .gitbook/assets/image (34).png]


_Fig 2. Placing base-station files into the folder shown above. The file types might be different_

**Pre-PPK Notes:**

* Do not close any pop-up cmd prompt or terminal windows (this is due to the application running a subprocess necessary for PPK-ing)
* It's a good habit to check to ensure that the original geotags on a couple of the photos somewhat correspond to the image location.
  * To do this: Use an exif inspection tool, grab the geotag from an image, search up coordinates on Google Earth, compare to see if the photo content somewhat matches up with coordinates on Google earth
  * If the images do not align, it might be a good idea to get the flight log (.ulog) file from the mission and use the Use ULOG workflow in the Freefly PPK app to get proper alignment.&#x20;

**Freefly PPK Processing:**

1. Open FreeflyPPK application.
2. Click on browse at the top to choose the Astro Map mission and select the folder.
3. The application should browse the folder and search for the requirements and automatically fill in all of the requirements.&#x20;

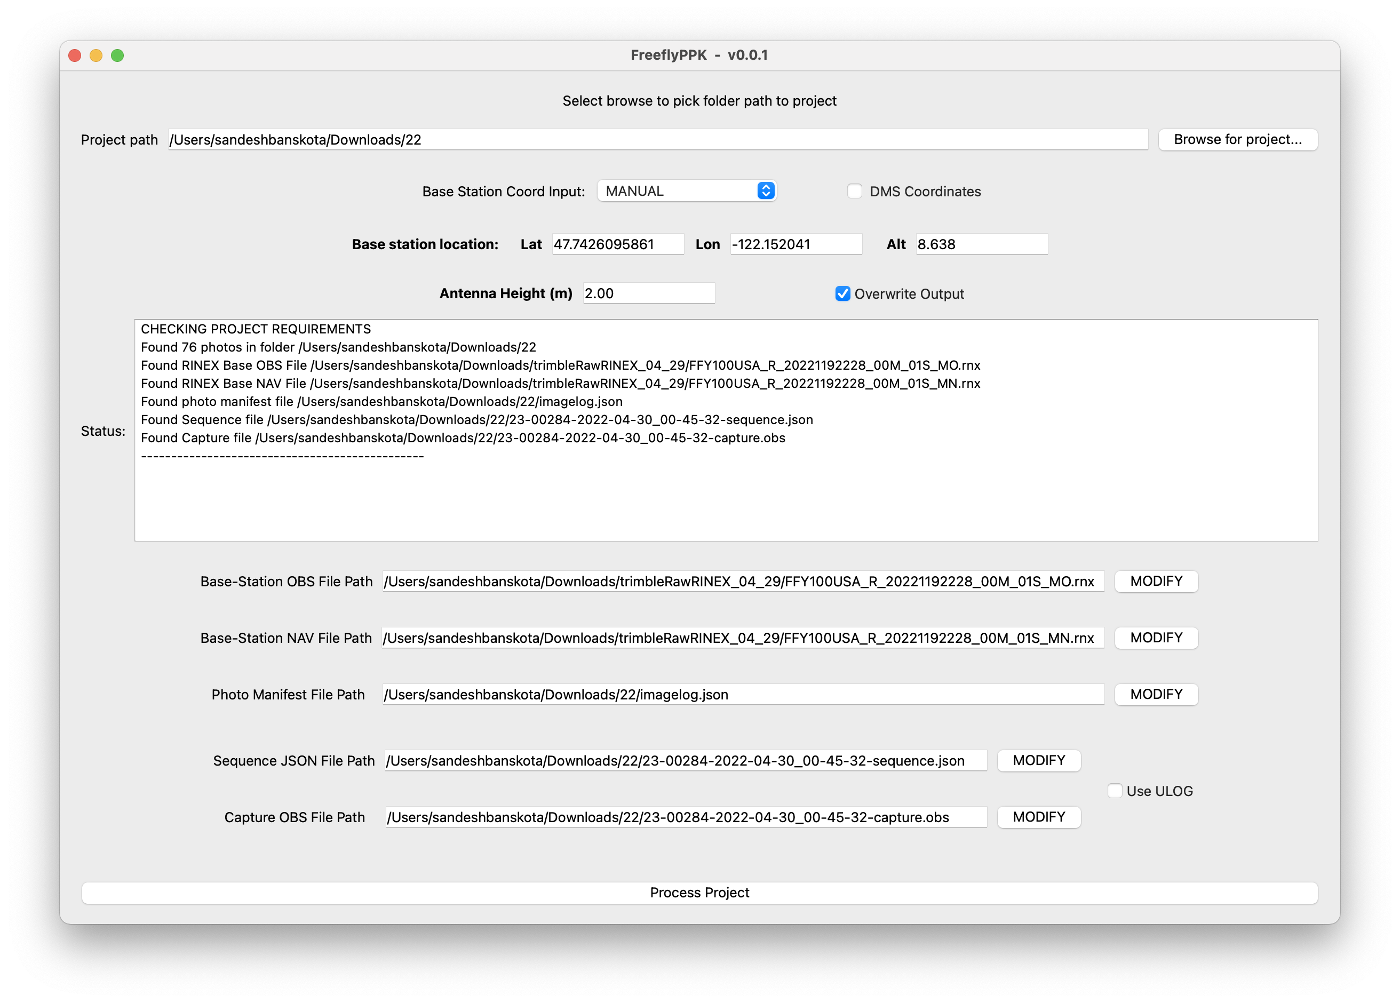
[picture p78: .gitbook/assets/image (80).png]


4\. If you know where the base station ground coordinate was, then enter it. This can be done using a GNSS reference network processing provider (i.e. in Washington state you can use Washington State Reference Network, in the U.S. you can use NOAA CORS and upload your base RINEX files)  You can use either DMS or Decimal coordinates (Click the `DMS Coordinates` check-box.)

5\. If you don't know the base station coordinate, by changing from `MANUAL` on the drop down to `AVERAGE FROM OBS` you can get a very rough estimate of the base station. It applies single point positioning to the base station RINEX files. The averaged postion will be displayed on the status bar once the project processing begins.

6\. Go ahead and select how high you placed the receiver from the ground (usually your base station tripod pole will have a marking to let you know). The application will take care of antenna phase center variation based on the base-station type detected from the base-station OBS file.&#x20;

7\. If you are rerunning the same mapping mission folder, checking the Overwrite Output check-box will overwrite the output folder with the current processing output. It is set to overwrite on default since the application can otherwise keep on making copy of the photos and take a lot of space on your computer. If the Overwrite Output check-box is not checked, then the application will rename the previous folder and save the output of the current processing to PPK\__Photos. \*TIP: you want to explore output with multiple settings (i.e. different base station coordinates or base station files), it might be beneficial to rename the PPK\_Photos folder to something more useful\*_

8\. Once all of the project requirements are met, you will be able to click the Process button and the application will correct the geotags on your photos after it conducts PPK on them. It will output them into the PPK\_Photos folder and keep your original images untouched. Monitor the output and ensure all or most of the photos are tagged with Q=1 quality. The Q value corresponds to the quality of the corrected geotag. Q=1 is great. Q=2 is ok. Anything higher is not accurate.

9\. Once your images are PPK-ed, you can use a map generation provider like ESRI Sitescan (which is recommended and we have tested on) and upload the images from the PPK\_Photos folder. In the Advanced Processing Settings:

* If you completed the PPK process with a surveyed point or reference network, use the +/- margin of error they provided to you in the base station location for the geolocation accuracy.
* If you use the AVERAGE OBS FILE option in the FreeflyPPK app, use +/- 100 cm. Note that it is not recommended to run AVERAGE OBS if you want high fidelity maps.&#x20;

**Debugging Tips:**

* Known Issue: If drone is flying below sealevel or drone is flying at negative altitude in the chosen base-station coordinate system, then the application will fail the geotagging process (status list error). This will be fixed in a future release.
* If you entered base station coordinates in Degrees, Minute, Second format, make sure you use the correct sign. i.e. If the coordinate you are entering is 122° 09' 7.93789" W, on Freefly PPK, you should enter -122  09  7.93789&#x20;
* If the correct base station file is not be detected correctly, remove all of the base files from inside of the project path folder. Then, individually go into modify the selected base and rinex files using the modify buttons below the status box. Check content inside the base files for "Observation" and "Navigation" to ensure you are choosing the correct files.
* One of the first debugging things you can do is to close the application and reopen it. More advanced users can go in and delete the .ppk\_history file in their home directory to remove application cache file. &#x20;
* Check to see if the rtkdata\_events.pos in the working directory has been generated properly. If everything looks good there, but there is an issue with photo tagging. (i.e. "Issue with abc.jpg tagging" alert, then there is likely an error with your filesystems (see common file systems error).
* Common file systems errors: Not enough space on your hard drive. Make sure the project path has plenty of space. A bunch of 25MP images can fill up your storage device quickly. Again, as previously mentioned, you will get much better performance if your project folder is in your local hard-drive instead of an extenal drive.
* If you have any issues with Freefly PPK and have questions for Freefly Support team, it would help if you sent as many of your files as you are able to (i.e content of working directory, capture.obs, sequence.json, and base-directory folder). It helps to include a screenshot of the application during an error, but ensure you expand the status list so that the whole error is visible in the photo. Since this is our first release of Freefly PPK software, we are actively working to improve the user experience based on feedback. &#x20;

## Precise Flight&#x20;

Precise Flight by Auterion is an alternative option for the PPK workflow. It can be downloaded from the App Store.&#x20;

### Compatible Devices:

iOS devices - primarily useful with iPad

### Precise Flight by Auterion Workflow

* Set up base station and get it recording
* Fly mission with astro, wait for it to finish processing photos after landing
  1. Shutoff astro
* Pull usb stick, and place into ipad
* Go to files app, browse to usb stick, and determine which folder has the files from this scan. I.e. folder 58
* Open emlid app
  1. Stop logging all 3 logs (position, raw data, base correction)
  2. After they are zipped
  3. Download all 3 files to the usb stick in the same directory as the scan
* Extract data
  1. Go to files app
  2. Browse to the folder with the photos in them
  3. Click once on the zip file with the emlid raw RINEX data in it to unzip
  4. It will create a folder in that directory
* Delete old data?
* Go to preciseflight app
  1. Select base station folder, will be the RINEX directory inside of the flight folder
  2. Select the vehicle folder- it is the folder with your mission number such as “58” that has the photos in it
  3. Decide if you want to set base position manually, enter as desired
  4. Enable compensate camera offset
  5. Hit process, wait the 30-60 seconds for processing
  6. When processing is complete, the files will be located in the Auterion Precise Flight app on the ipad (not on the USB stick).&#x20;
  7. When working properly, Sitescan app can be pointed at that folder to upload the photos
  8. I’ve been using files app to copy the PPK’d photos  into a new folder on the usb drive and then transferring to computer.

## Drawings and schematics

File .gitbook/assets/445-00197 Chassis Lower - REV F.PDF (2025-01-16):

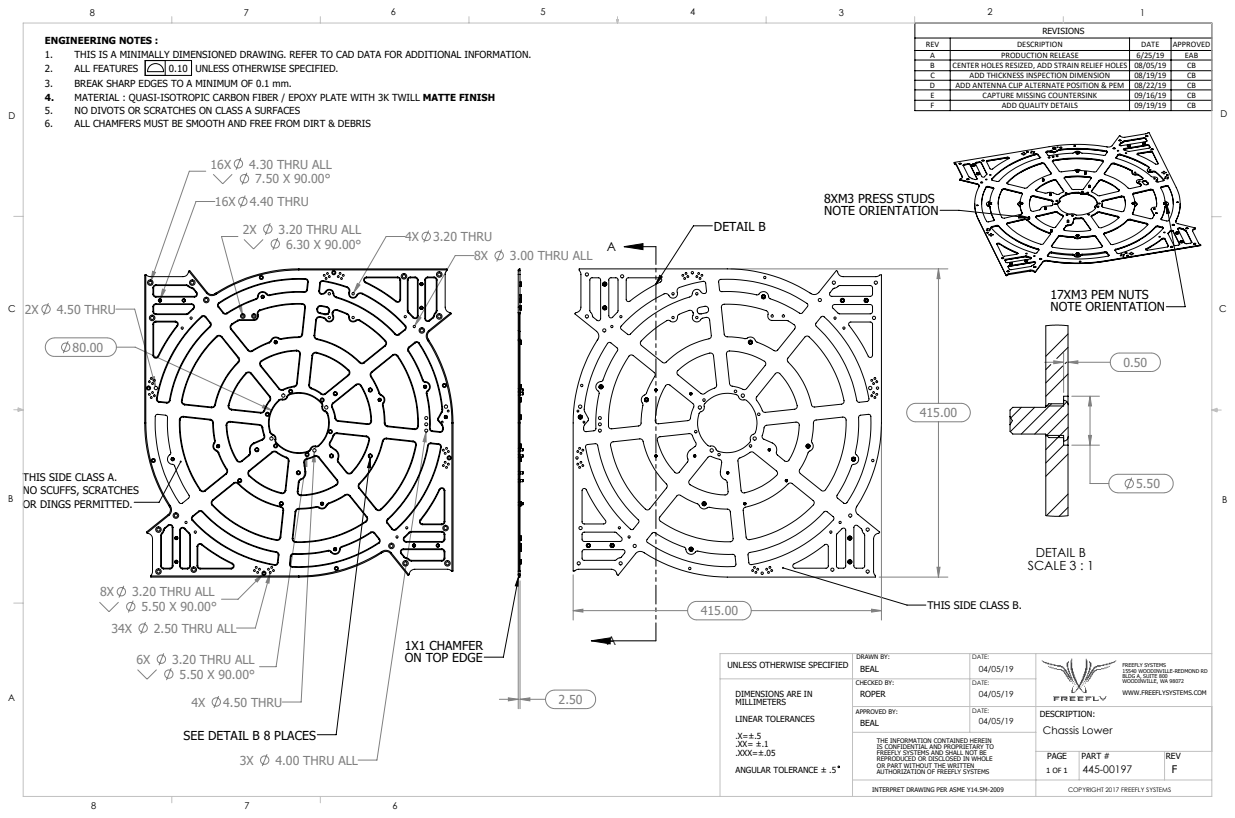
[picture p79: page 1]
DETAIL B; 17XM3 PEM NUTS NOTE ORIENTATION; 8XM3 PRESS STUDS NOTE ORIENTATION; DETAIL B SCALE 3 : 1; 16X 4.30 THRU ALL 7.50 X 90.00° 16X 4.40 THRU; 8X 3.20 THRU ALL 5.50 X 90.00°; 2.50 THRU ALL; 2X 4.50 THRU; 3.20 THRU ALL; 4X 3.20 THRU; 4.00 THRU ALL; 4X 4.50 THRU; 3.00 THRU ALL; SEE DETAIL B 8 PLACES; ALL FEATURES; UNLESS OTHERWISE SPECIFIED.; DIMENSIONS ARE IN; LINEAR TOLERANCES; ANGULAR TOLERANCE ± .5; Chassis Lower; PART #; REV; DESCRIPTION: DATE:; APPROVED BY:; CHECKED BY:; DRAWN BY:

ENGINEERING NOTES :
1. THIS IS A MINIMALLY DIMENSIONED DRAWING. REFER TO CAD DATA FOR ADDITIONAL INFORMATION.
3. BREAK SHARP EDGES TO A MINIMUM OF 0.1 mm.
4. MATERIAL : QUASI-ISOTROPIC CARBON FIBER / EPOXY PLATE WITH 3K TWILL MATTE FINISH
5. NO DIVOTS OR SCRATCHES ON CLASS A SURFACES
6. ALL CHAMFERS MUST BE SMOOTH AND FREE FROM DIRT & DEBRIS

REV | DESCRIPTION | DATE | APPROVED
A | PRODUCTION RELEASE | 6/25/19 | EAB
B | CENTER HOLES RESIZED, ADD STRAIN RELIEF HOLES | 08/05/19 | CB
C | ADD THICKNESS INSPECTION DIMENSION | 08/19/19 | CB
D | ADD ANTENNA CLIP ALTERNATE POSITION & PEM | 08/22/19 | CB
E | CAPTURE MISSING COUNTERSINK | 09/16/19 | CB
F | ADD QUALITY DETAILS | 09/19/19 | CB

THIS SIDE CLASS A.
NO SCUFFS, SCRATCHES
OR DINGS PERMITTED.

THIS SIDE CLASS B.

1X1 CHAMFER
ON TOP EDGE

UNLESS OTHERWISE SPECIFIED

FREEFLY SYSTEMS
15540 WOODINVILLE-REDMOND RD
BLDG A, SUITE 800
WOODINVILLE, WA 98072
WWW.FREEFLYSYSTEMS.COM

THE INFORMATION CONTAINED HEREIN
IS CONFIDENTIAL AND PROPRIETARY TO
FREEFLY SYSTEMS AND SHALL NOT BE
REPRODUCED OR DISCLOSED IN WHOLE
OR PART WITHOUT THE WRITTEN
AUTHORIZATION OF FREEFLY SYSTEMS

INTERPRET DRAWING PER ASME Y14.5M-2009

COPYRIGHT 2017 FREEFLY SYSTEMS

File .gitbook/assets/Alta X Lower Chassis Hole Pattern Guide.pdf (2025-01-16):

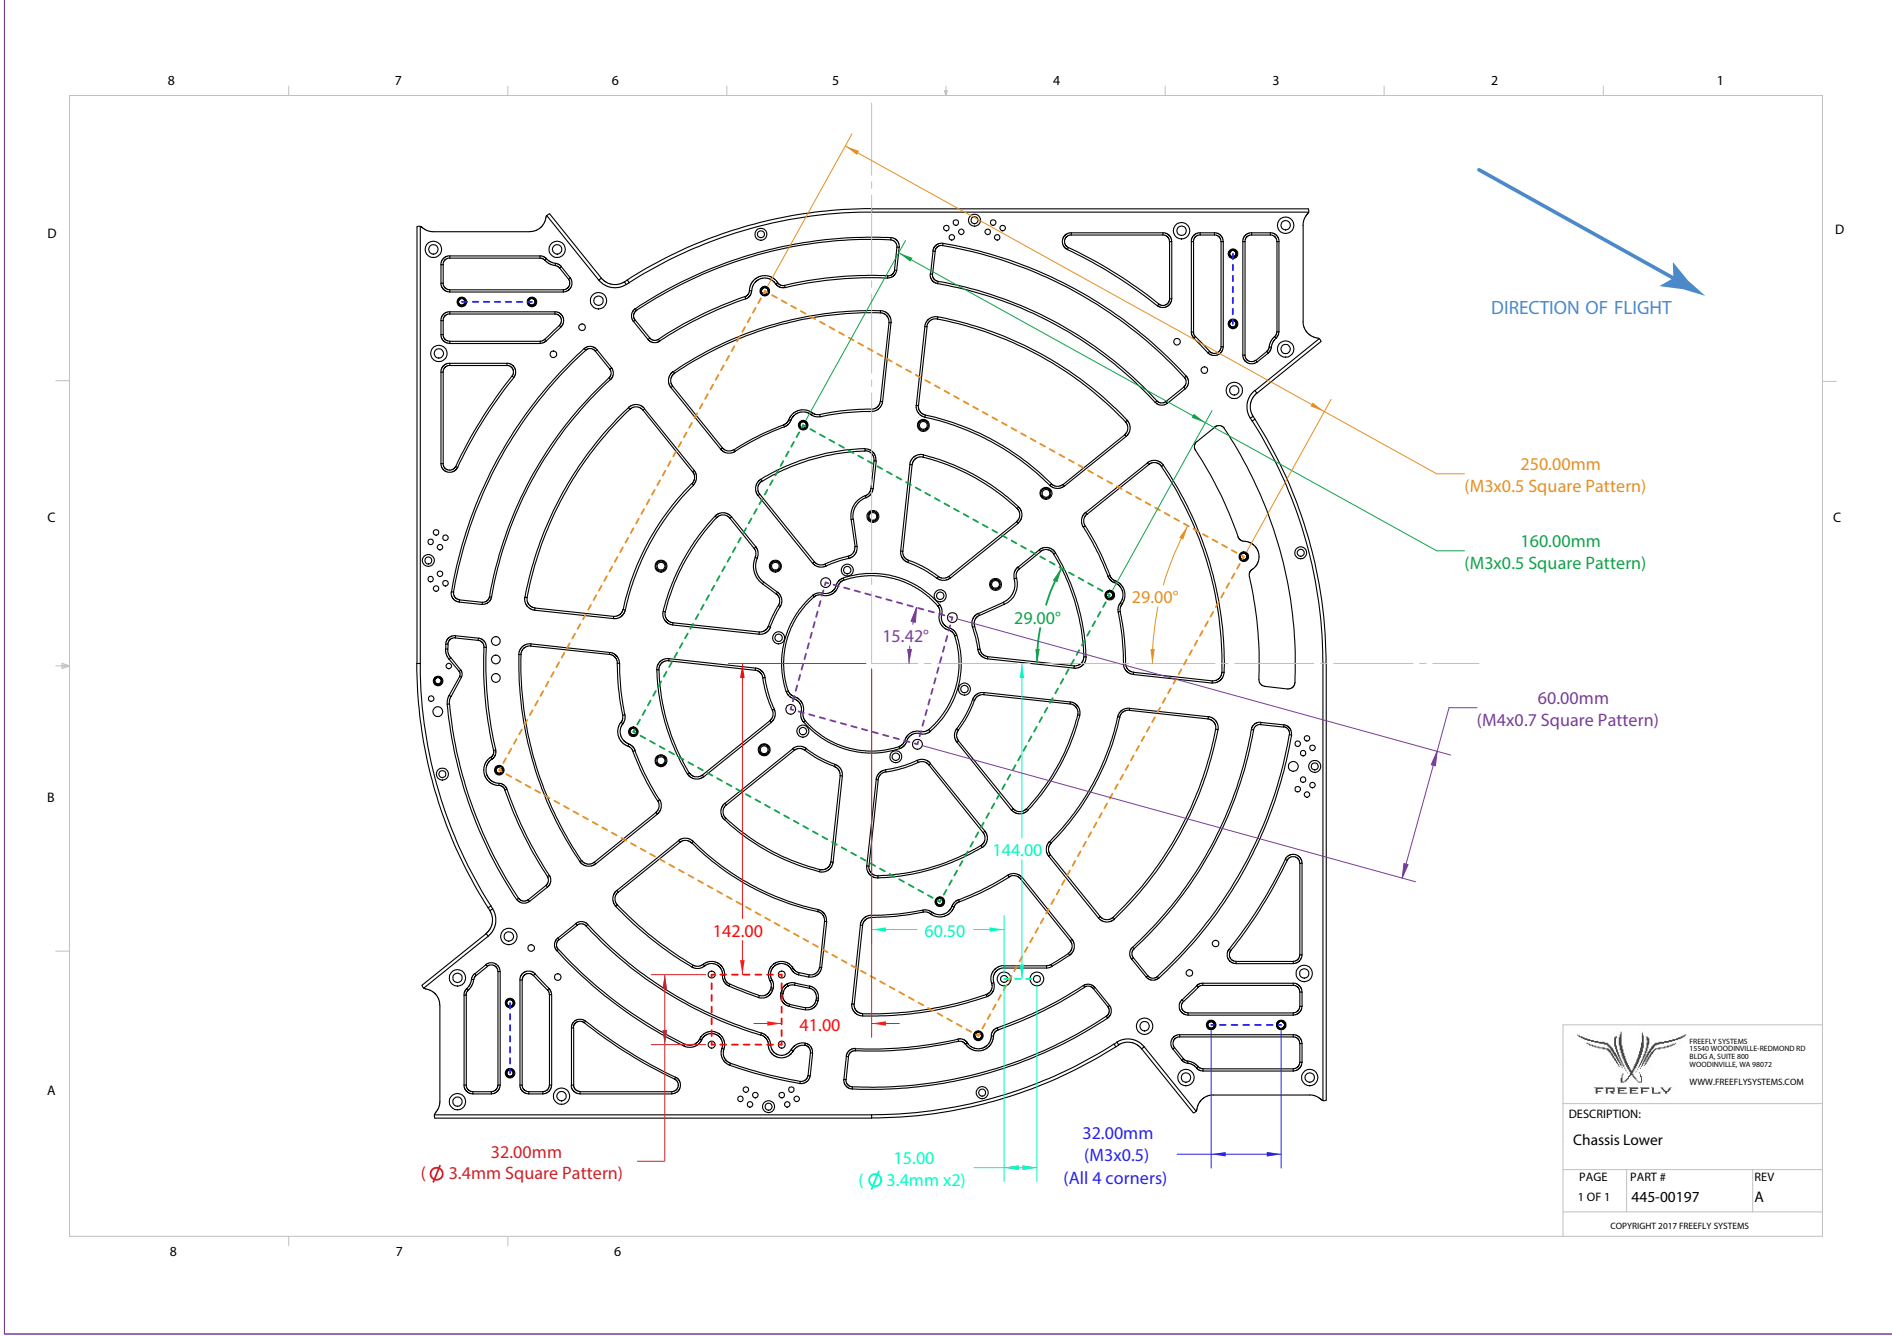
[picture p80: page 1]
160.00mm (M3x0.5 Square Pattern); 32.00mm ( 3.4mm Square Pattern); 60.00mm (M4x0.7 Square Pattern); 250.00mm (M3x0.5 Square Pattern); (M3x0.5) (All 4 corners); DESCRIPTION:; Chassis Lower; PAGE; PART #; REV

DIRECTION OF FLIGHT

FREEFLY SYSTEMS
15540 WOODINVILLE-REDMOND RD
BLDG A, SUITE 800
WOODINVILLE, WA 98072
WWW.FREEFLYSYSTEMS.COM

COPYRIGHT 2017 FREEFLY SYSTEMS

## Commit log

2025-01-16 "Show Distance Sensor App Output" -> "Show Distance Sensor App Data" (AMC v1.34.11)
    [ALPHA_410-01094 Dovetail Mount Universal with Passthrough.STEP]
2025-01-24 No subject
    [432-00086 Antenna Mount Astro REV_01.STEP, 432-00086 Antenna Mount Astro REV_01.STL]
2026-02-10 Added usage for Bind Button on Astro
2026-02-26 Adding logic voltage spec to payload adapter uart
2026-05-20 LR1 camera upgrade link
2026-05-28 fixed broken table on Astro LED status
2026-06-05 Astro antenna positioning images edited
2026-06-19 added legacy vs max props to replacing props guide
2026-06-19 added propeller link to components page
2026-06-25 Fixed CAD links
    [Astro FPV System.STL, Flux GNSS Module and Astro Mount.STL]
